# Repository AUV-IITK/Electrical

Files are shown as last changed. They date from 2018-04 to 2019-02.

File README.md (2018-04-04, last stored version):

# Hyperion-Electrical

The repo contains all the schematics, PCB designs, simulations and other files related to Electrical subsystem of AUV-IITK including both past and current projects. A short description of every subdirectory is provided below in the reverse chronological order.

## actuator_board_v1.0 
The team is set to design and fabricate a single PCB for all the drivers that are needed for the actuators in the vehicle. The board also contains a slightly modified version and custom layout of Arduino Mega 2560's [reference design](https://www.arduino.cc/en/uploads/Main/arduino-mega2560-schematic.pdf?). Other than that, the following components form the crux of the board:

[MC34932](https://www.nxp.com/docs/en/data-sheet/MC34932.pdf) Dual H-Bridge Motor Driver to drive [BTD150 Thrusters](http://ocean-innovations.net/OceanInnovationsNEW/SeaBotix/BTD150_Data_Sheet.pdf) from SeaBotix

[Basic ESC R3](http://docs.bluerobotics.com/bescr3/) ESC from BlueRobotics to drive [T200 Thrusters](https://www.bluerobotics.com/store/thrusters/t200-thruster/) also from BlueRobotics

[DRV102](http://www.ti.com/product/DRV102) PWM Solenoid driver from Texas Instruments to control solenoid operated valves

## actuator_board_v0.1
This board is a prototype board intended to test the [MC34932](https://www.nxp.com/docs/en/data-sheet/MC34932.pdf) motor drivers and [Atmega2560](http://ww1.microchip.com/downloads/en/DeviceDoc/Atmel-2549-8-bit-AVR-Microcontroller-ATmega640-1280-1281-2560-2561_datasheet.pdf) circuit independently and observe their individual behavior before integrating them into v1.0 board. The board was fabricated and tested and it worked successfully. The team is moved onto designing the v1.0 board.

## BMSv2
This board is a concept-design of a Battery Management System to control, monitor and protect the Lithium Polymer batteries used in the vehicle. This board has not been fabricated due to technical difficulties we faced while testing the ICs. The following components are used in the board:

[Atxmega128A1U](http://ww1.microchip.com/downloads/en/DeviceDoc/Atmel-8385-8-and-16-bit-AVR-Microcontroller-ATxmega64A1U-ATxmega128A1U_datasheet.pdf) microcontroller as the brain of the board

[BQ76930](http://www.ti.com/lit/ds/symlink/bq76920.pdf) and [BQ78350-R1](https://www.ti.com/lit/ds/symlink/bq78350-r1.pdf?HQS=TI-null-null-sf-df-ds-null-wwe) battery management ICs from Texas Instruments

[TPS54531](http://www.ti.com/lit/ds/symlink/tps54531.pdf) Step Down DC-DC converters to create two voltage rails at 3.3V (to power the Atxmega chip) and 15V (To power an [Intel NUC](https://www.intel.in/content/www/in/en/products/boards-kits/nuc/kits/nuc5i7ryh.html) which is the main on-board computer in the vehicle). The board also provides an unregulated rail to power the [BTD150 Thrusters](http://ocean-innovations.net/OceanInnovationsNEW/SeaBotix/BTD150_Data_Sheet.pdf)

[ACS725](https://www.allegromicro.com/en/Products/Current-Sensor-ICs/Zero-To-Fifty-Amp-Integrated-Conductor-Sensor-ICs/ACS725.aspx) Current Sensors to monitor the current in each of the three rails

## BMS
This is a rudimentary battery management board that was created to act as a back-plane to connect multiple third-party modules. The board has been fabricated and tested and it worked succesfully. The board, however, didn't make it into the vehicle due to its large size.

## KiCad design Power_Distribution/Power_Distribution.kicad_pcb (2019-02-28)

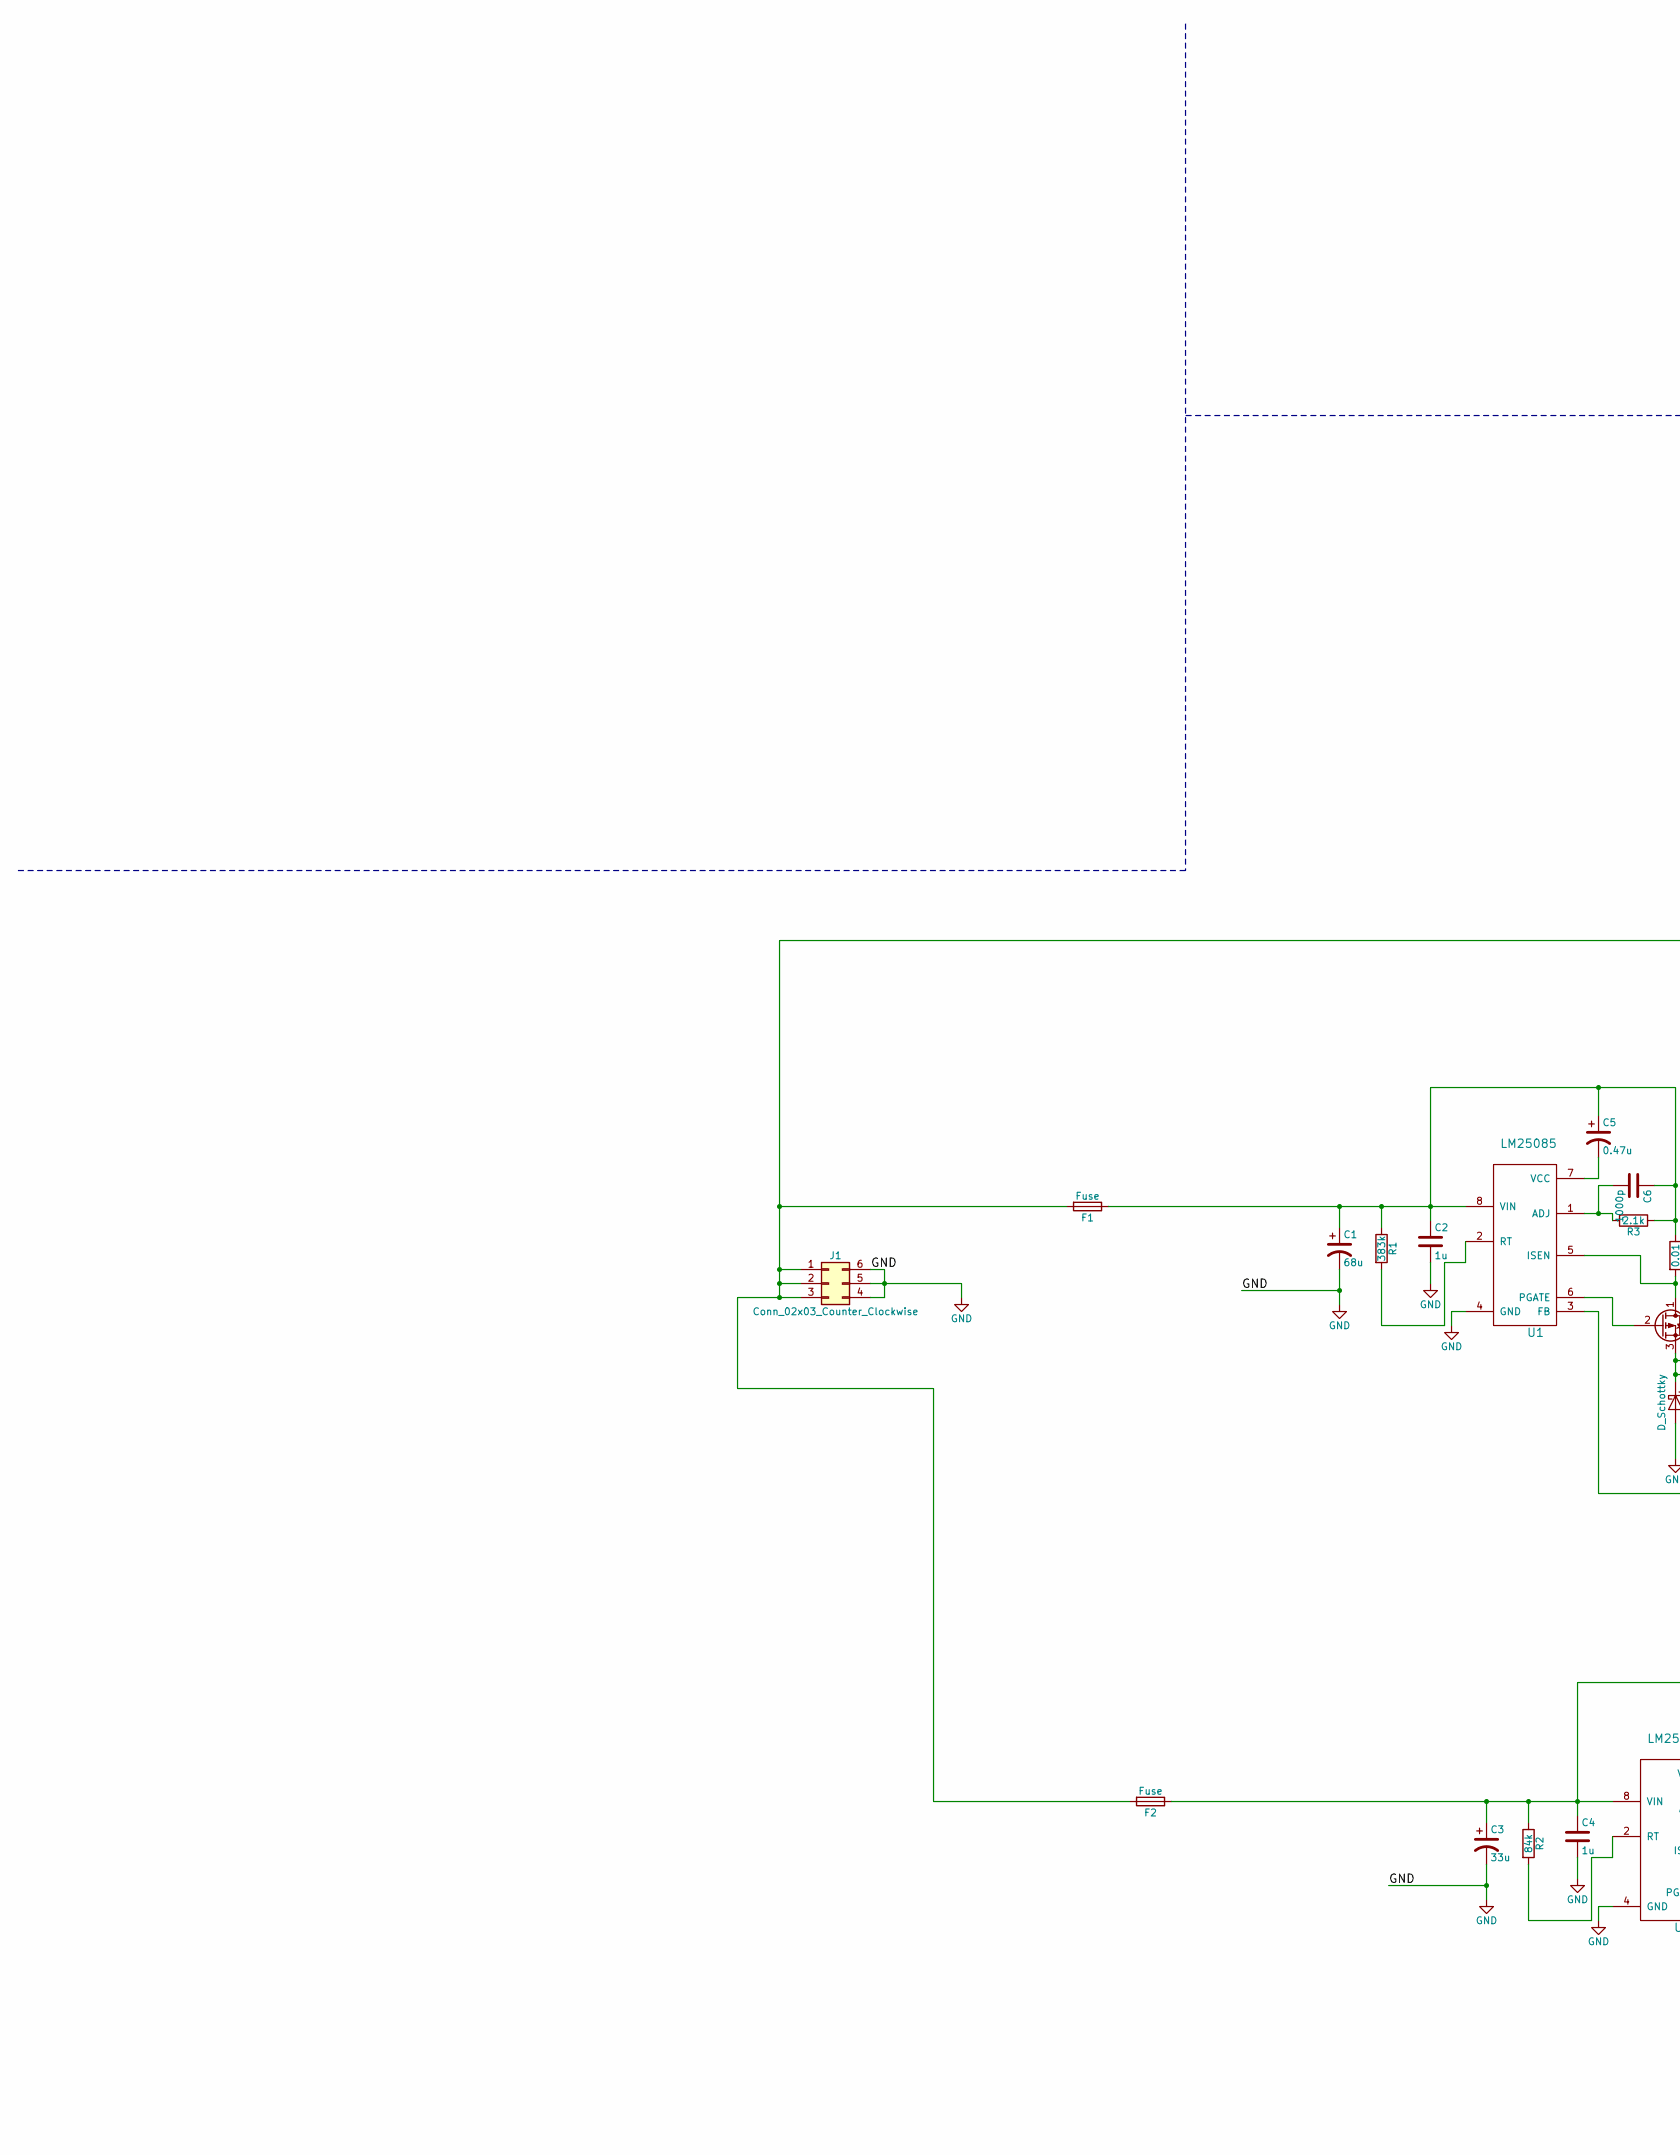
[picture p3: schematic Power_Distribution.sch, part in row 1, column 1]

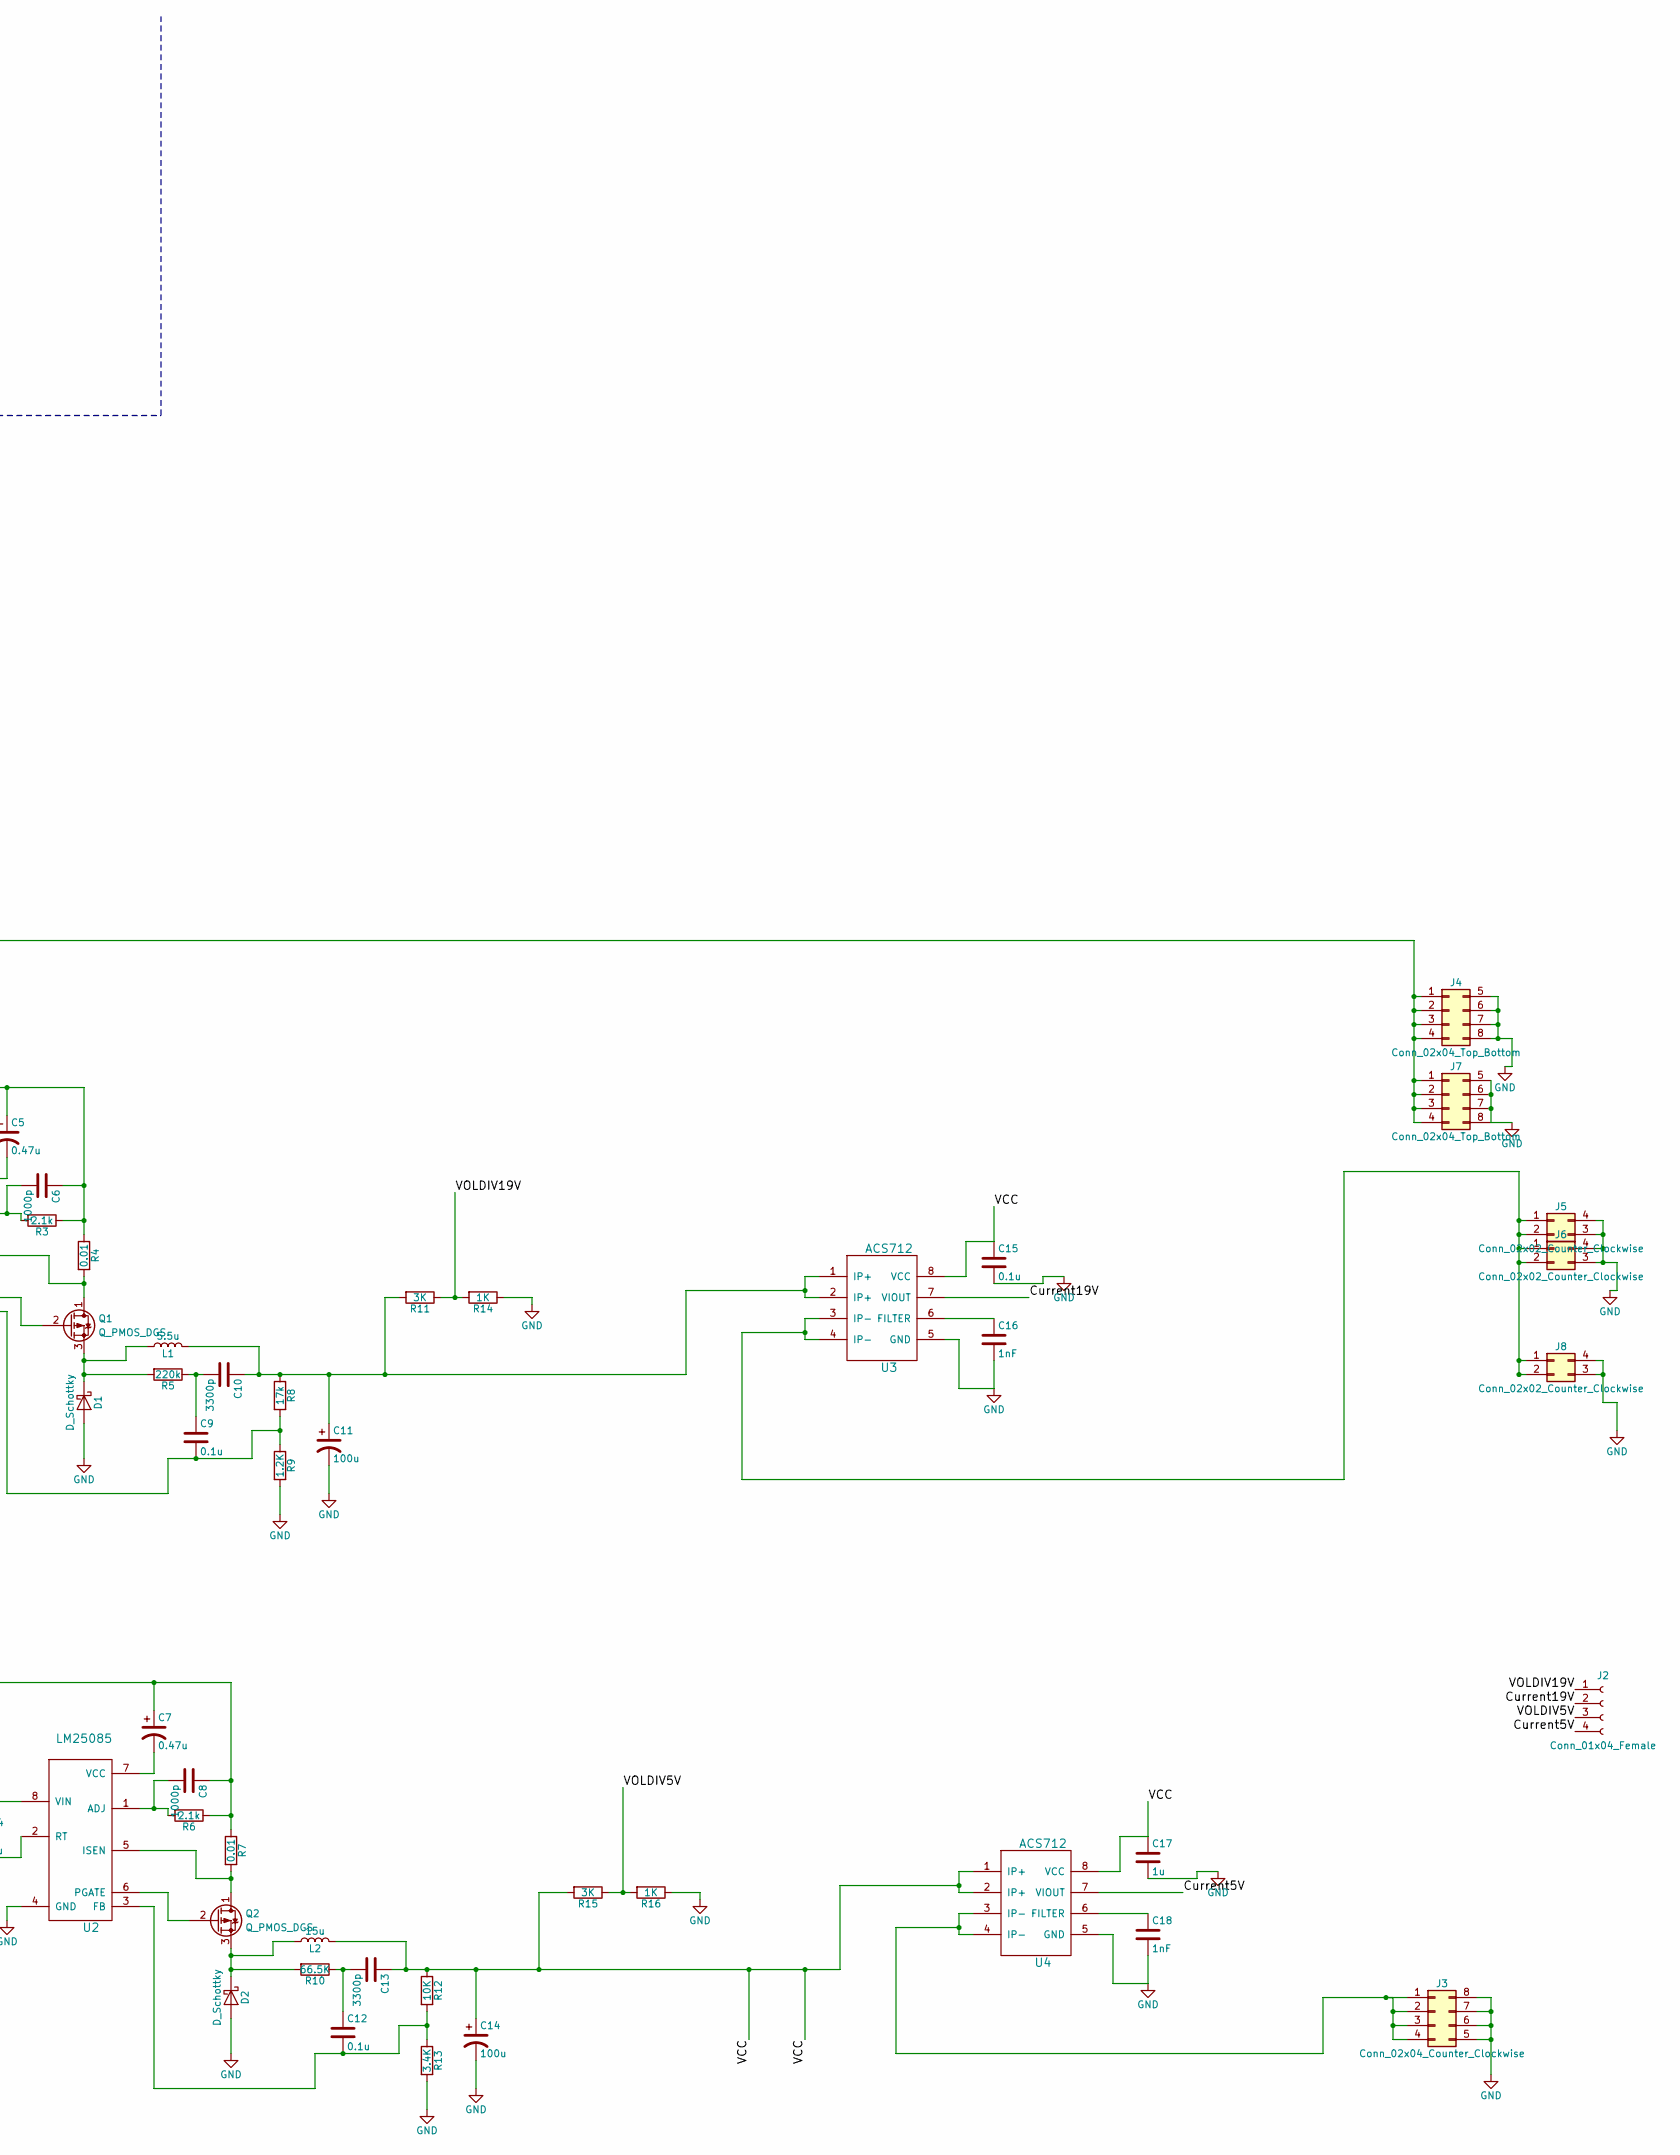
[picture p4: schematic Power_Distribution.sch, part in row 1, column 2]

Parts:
C1: 68u; CP_Radial_D6.3mm_P2.50mm
C2, C4, C17: 1u; C_1206
C3: 33u; CP_Radial_D6.3mm_P2.50mm
C5, C7: 0.47u; CP_Radial_D5.0mm_P2.00mm
C6, C8: 1000p; C_1206
C9, C12, C15: 0.1u; C_1206
C10, C13: 3300p; C_1206
C11, C14: 100u; CP_Radial_D8.0mm_P3.50mm
C16, C18: 1nF; C_1206
D1, D2: D_Schottky; TO-220-2_Vertical
F1, F2: Fuse; Fuse_SMD1206_Wave
J1: Conn_02x03_Counter_Clockwise; Molex_MegaFit_2x03x5.70mm_Straight
J2: Conn_01x04_Female; Molex_PicoClasp_501331-0407_1x04_P1.0mm_Vertical
J3: Conn_02x04_Counter_Clockwise; Molex_MegaFit_2x04x5.70mm_Straight
J4, J7: Conn_02x04_Top_Bottom; Molex_MegaFit_2x04x5.70mm_Straight
J5, J6, J8: Conn_02x02_Counter_Clockwise; Molex_MegaFit_2x02x5.70mm_Straight
L1: 5.5u; L_10.4x10.4_H4.8
L2: 15u; inductor_13.5x12.5
Q1, Q2: Q_PMOS_DGS; TO-252-3_TabPin2
R1: 383k; R_1206
R2: 84k; R_1206
R3, R6: 2.1k; R_1206
R4, R7: 0.01; R_1206
R5: 220k; R_1206
R8: 17k; R_1206
R9: 1.2K; R_1206
R10: 66.5K; R_1206
R11, R15: 3K; R_1206
R12: 10K; R_1206
R13: 3.4K; R_1206
R14, R16: 1K; R_1206
U1, U2: LM25085; VSSOP-8_3.0x3.0mm_Pitch0.65mm
U3, U4: ACS712; SOIC-8_3.9x4.9mm_Pitch1.27mm

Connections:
/Current5V: J2.4, U4.7 (VIOUT)
/Current19V: J2.2, U3.7 (VIOUT)
/VCC: C13.1, C14.1, C15.1, C17.1, L2.2, R12.1, R15.2, U3.8 (VCC), U4.1 (IP+), U4.2 (IP+), U4.8 (VCC)
/VOLDIV5V: J2.3, R15.1, R16.2
/VOLDIV19V: J2.1, R11.1, R14.2
GND: C1.2, C2.2, C3.2, C4.2, C11.2, C14.2, C15.2, C16.2, C17.2, C18.2, D1.2 (A), D2.2 (A), J1.4, J1.5, J1.6, J3.5, J3.6, J3.7, J3.8, J4.5, J4.6, J4.7, J4.8, J5.3, J5.4, J6.3, J6.4, J7.5, J7.6, J7.7, J7.8, J8.3, J8.4, R9.2, R13.2, R14.1, R16.1, U1.4 (GND), U2.4 (GND), U3.5 (GND), U4.5 (GND)
unnamed: C1.1, C2.1, C5.1, C6.1, F1.1, R1.1, R3.1, R4.1, U1.8 (VIN)
unnamed: C3.1, C4.1, C7.1, C8.1, F2.1, R2.1, R6.1, R7.1, U2.8 (VIN)
unnamed: C5.2, U1.7 (VCC)
unnamed: C6.2, R3.2, U1.1 (ADJ)
unnamed: C7.2, U2.7 (VCC)
unnamed: C8.2, R6.2, U2.1 (ADJ)
unnamed: C9.2, R8.2, R9.1, U1.3 (FB)
unnamed: C10.1, C11.1, L1.2, R8.1, R11.2, U3.1 (IP+), U3.2 (IP+)
unnamed: C9.1, C10.2, R5.1
unnamed: C12.1, C13.2, R10.1
unnamed: C12.2, R12.2, R13.1, U2.3 (FB)
unnamed: C16.1, U3.6 (FILTER)
unnamed: C18.1, U4.6 (FILTER)
unnamed: D1.1 (K), L1.1, Q1.3 (S), R5.2
unnamed: D2.1 (K), L2.1, Q2.3 (S), R10.2
unnamed: F1.2, F2.2, J1.1, J1.2, J1.3, J4.1, J4.2, J4.3, J4.4, J7.1, J7.2, J7.3, J7.4
unnamed: J3.1, J3.2, J3.3, J3.4, U4.3 (IP-), U4.4 (IP-)
unnamed: J5.1, J5.2, J6.1, J6.2, J8.1, J8.2, U3.3 (IP-), U3.4 (IP-)
unnamed: Q1.1 (D), R4.2, U1.5 (ISEN)
unnamed: Q1.2 (G), U1.6 (PGATE)
unnamed: Q2.1 (D), R7.2, U2.5 (ISEN)
unnamed: Q2.2 (G), U2.6 (PGATE)
unnamed: R1.2, U1.2 (RT)
unnamed: R2.2, U2.2 (RT)

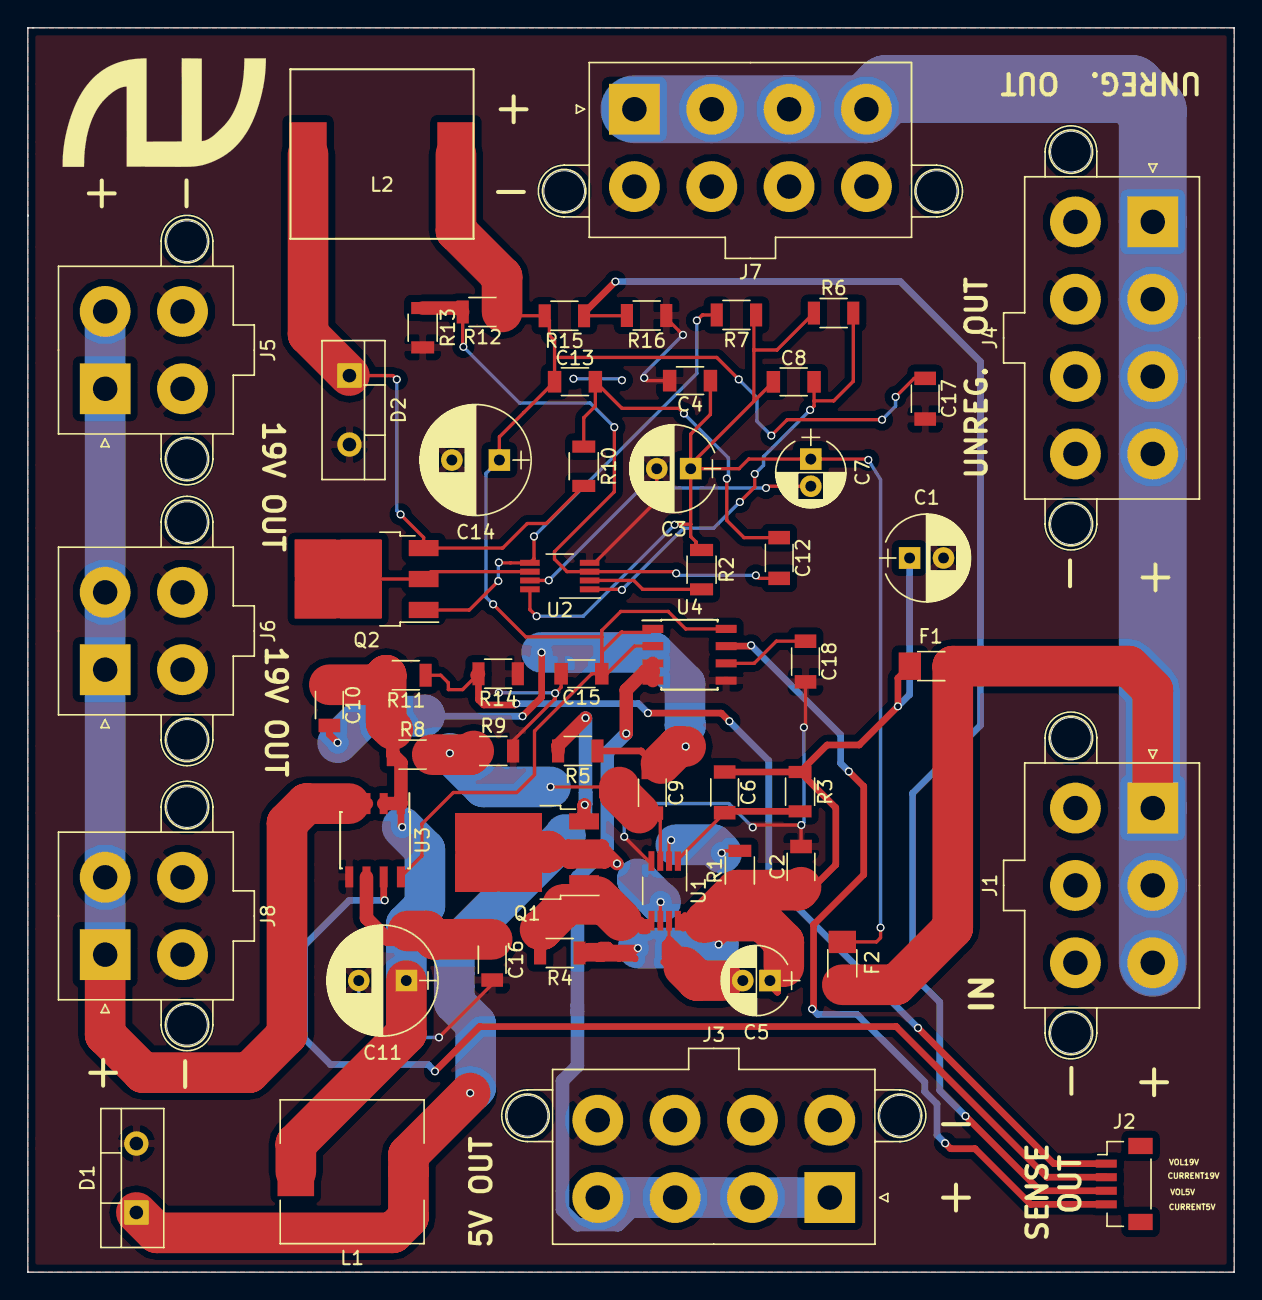
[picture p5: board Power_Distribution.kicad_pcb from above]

Board: 2 copper layers, 88.9 x 91.7 mm, 54 parts (0 on the bottom side), 30 nets.

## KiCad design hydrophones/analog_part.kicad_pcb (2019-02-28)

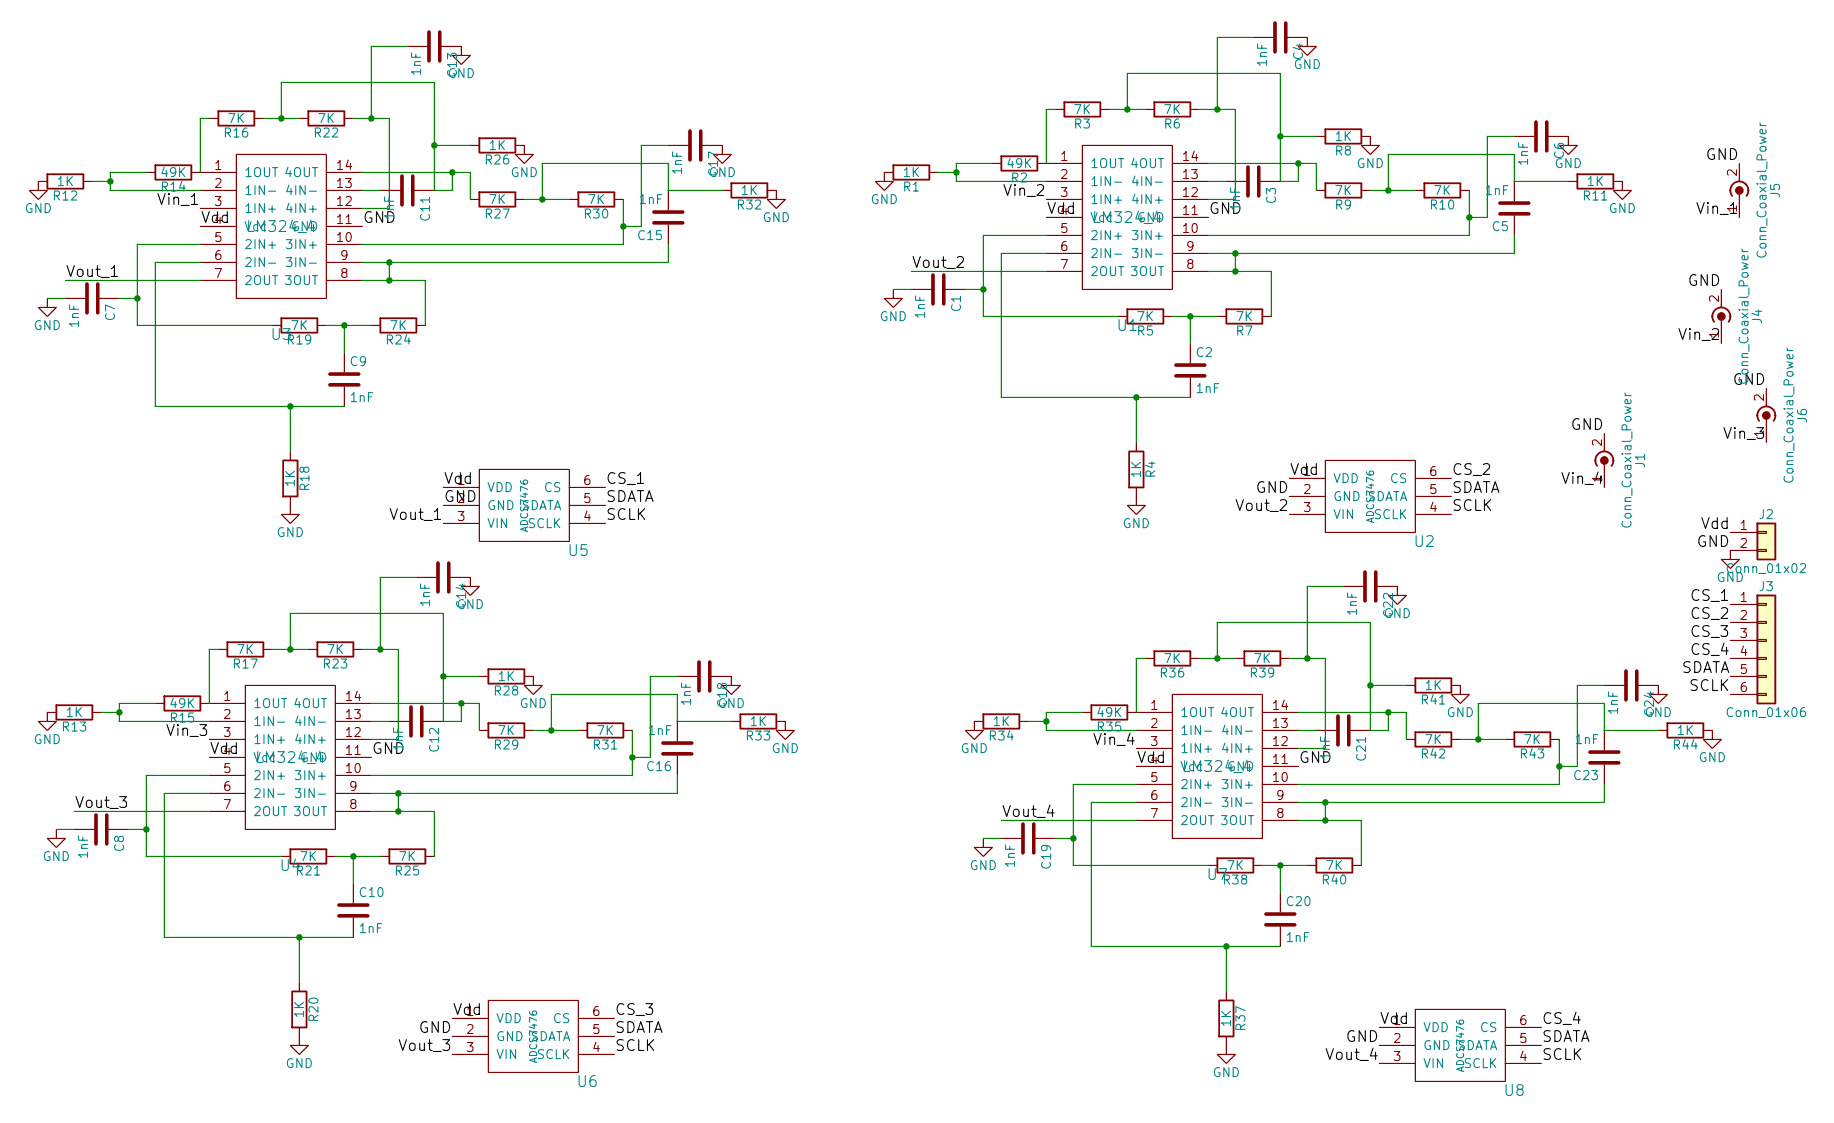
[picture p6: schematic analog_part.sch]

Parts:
C1, C2, C3, C4, C5, C6, C7, C8, C9, C10, C11, C12, C13, C14, C15, C16, C17, C18, C19, C20, C21, C22, C23, C24: 1nF; C_1206_HandSoldering
J1, J4, J5, J6: Conn_Coaxial_Power; bnc-ci
J2: Conn_01x02; Pin_Header_Angled_1x02_Pitch2.54mm
J3: Conn_01x06; Pin_Header_Angled_1x06_Pitch2.54mm
R1, R4, R8, R11, R12, R13, R18, R20, R26, R28, R32, R33, R34, R37, R41, R44: 1K; R_1206_HandSoldering
R2, R14, R15, R35: 49K; R_1206_HandSoldering
R3, R5, R6, R7, R9, R10, R16, R17, R19, R21, R22, R23, R24, R25, R27, R29, R30, R31, R36, R38, R39, R40, R42, R43: 7K; R_1206_HandSoldering
U1, U3, U4, U7: LM324_4; TSSOP-14_4.4x5mm_Pitch0.65mm
U2, U5, U6, U8: ADCS7476; SOT-23-6_Handsoldering

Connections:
/CS_1: J3.1, U5.6 (CS)
/CS_2: J3.2, U2.6 (CS)
/CS_3: J3.3, U6.6 (CS)
/CS_4: J3.4, U8.6 (CS)
/SCLK: J3.6, U2.4 (SCLK), U5.4 (SCLK), U6.4 (SCLK), U8.4 (SCLK)
/SDATA: J3.5, U2.5 (SDATA), U5.5 (SDATA), U6.5 (SDATA), U8.5 (SDATA)
/Vdd: J2.1, U1.4 (Vcc), U2.1 (VDD), U3.4 (Vcc), U4.4 (Vcc), U5.1 (VDD), U6.1 (VDD), U7.4 (Vcc), U8.1 (VDD)
/Vin_1: J5.1 (In), U3.3 (1IN+)
/Vin_2: J4.1 (In), U1.3 (1IN+)
/Vin_3: J6.1 (In), U4.3 (1IN+)
/Vin_4: J1.1 (In), U7.3 (1IN+)
/Vout_1: U3.7 (2OUT), U5.3 (VIN)
/Vout_2: U1.7 (2OUT), U2.3 (VIN)
/Vout_3: U4.7 (2OUT), U6.3 (VIN)
/Vout_4: U7.7 (2OUT), U8.3 (VIN)
GND: C1.2, C4.1, C6.1, C7.2, C8.2, C13.1, C14.1, C17.1, C18.1, C19.2, C22.1, C24.1, J1.2 (Ext), J2.2, J4.2 (Ext), J5.2 (Ext), J6.2 (Ext), R1.2, R4.2, R8.1, R11.1, R12.2, R13.2, R18.2, R20.2, R26.1, R28.1, R32.1, R33.1, R34.2, R37.2, R41.1, R44.1, U1.11 (GND), U2.2 (GND), U3.11 (GND), U4.11 (GND), U5.2 (GND), U6.2 (GND), U7.11 (GND), U8.2 (GND)
unnamed: C1.1, R5.2, U1.5 (2IN+)
unnamed: C2.1, R5.1, R7.2
unnamed: C2.2, R4.1, U1.6 (2IN-)
unnamed: C3.1, R3.1, R6.2, R8.2, R9.2, U1.14 (4OUT)
unnamed: C3.2, U1.13 (4IN-)
unnamed: C4.2, R6.1, U1.12 (4IN+)
unnamed: C5.1, R7.1, U1.8 (3OUT), U1.9 (3IN-)
unnamed: C5.2, R9.1, R10.2, R11.2
unnamed: C6.2, R10.1, U1.10 (3IN+)
unnamed: C7.1, R19.2, U3.5 (2IN+)
unnamed: C8.1, R21.2, U4.5 (2IN+)
unnamed: C9.1, R19.1, R24.2
unnamed: C9.2, R18.1, U3.6 (2IN-)
unnamed: C10.1, R21.1, R25.2
unnamed: C10.2, R20.1, U4.6 (2IN-)
unnamed: C11.1, R16.1, R22.2, R26.2, R27.2, U3.14 (4OUT)
unnamed: C11.2, U3.13 (4IN-)
unnamed: C12.1, R17.1, R23.2, R28.2, R29.2, U4.14 (4OUT)
unnamed: C12.2, U4.13 (4IN-)
unnamed: C13.2, R22.1, U3.12 (4IN+)
unnamed: C14.2, R23.1, U4.12 (4IN+)
unnamed: C15.1, R24.1, U3.8 (3OUT), U3.9 (3IN-)
unnamed: C15.2, R27.1, R30.2, R32.2
unnamed: C16.1, R25.1, U4.8 (3OUT), U4.9 (3IN-)
unnamed: C16.2, R29.1, R31.2, R33.2
unnamed: C17.2, R30.1, U3.10 (3IN+)
unnamed: C18.2, R31.1, U4.10 (3IN+)
unnamed: C19.1, R38.2, U7.5 (2IN+)
unnamed: C20.1, R38.1, R40.2
unnamed: C20.2, R37.1, U7.6 (2IN-)
unnamed: C21.1, R36.1, R39.2, R41.2, R42.2, U7.14 (4OUT)
unnamed: C21.2, U7.13 (4IN-)
unnamed: C22.2, R39.1, U7.12 (4IN+)
unnamed: C23.1, R40.1, U7.8 (3OUT), U7.9 (3IN-)
unnamed: C23.2, R42.1, R43.2, R44.2
unnamed: C24.2, R43.1, U7.10 (3IN+)
unnamed: R1.1, R2.2, U1.2 (1IN-)
unnamed: R2.1, R3.2, U1.1 (1OUT)
unnamed: R12.1, R14.2, U3.2 (1IN-)
unnamed: R13.1, R15.2, U4.2 (1IN-)
unnamed: R14.1, R16.2, U3.1 (1OUT)
unnamed: R15.1, R17.2, U4.1 (1OUT)
unnamed: R34.1, R35.2, U7.2 (1IN-)
unnamed: R35.1, R36.2, U7.1 (1OUT)

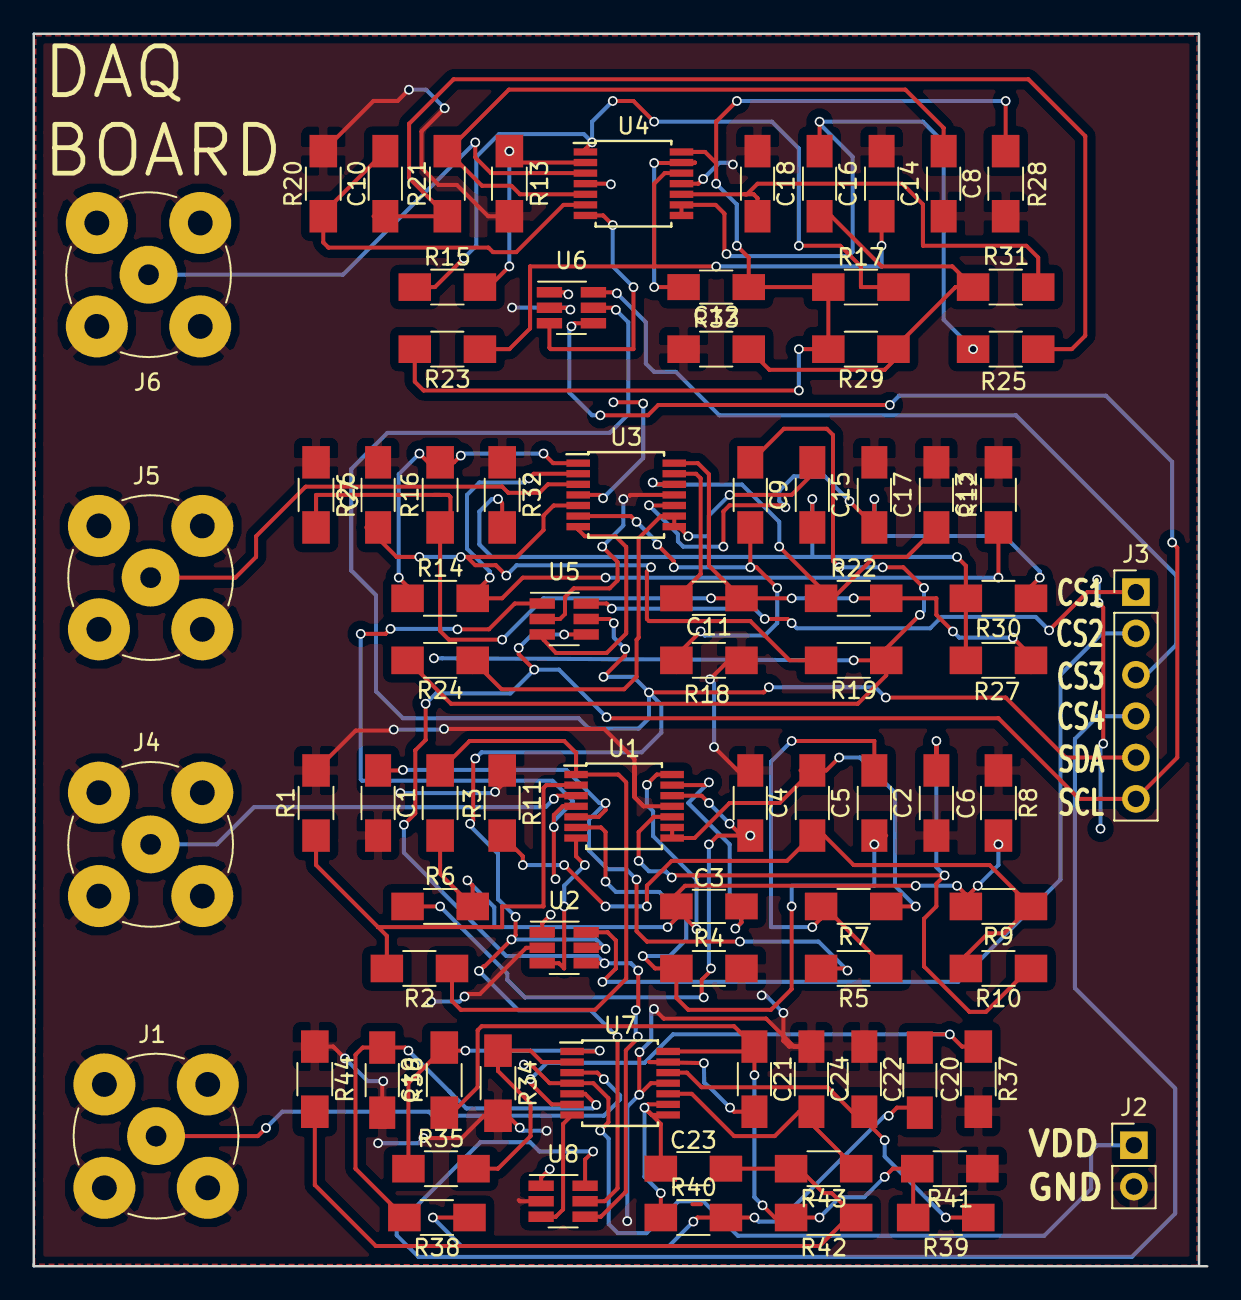
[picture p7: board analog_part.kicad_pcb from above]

Board: 2 copper layers, 72.1 x 75.7 mm, 82 parts (0 on the bottom side), 60 nets.

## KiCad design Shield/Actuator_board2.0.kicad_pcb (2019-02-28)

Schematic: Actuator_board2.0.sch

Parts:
J1: Conn_01x05_Male; Pin_Header_Straight_1x05_Pitch2.54mm
J2, J3: Conn_01x13_Female; Socket_Strip_Straight_1x13_Pitch2.54mm
J4, J5, J8, J9, J12: Conn_01x04_Male; Pin_Header_Straight_1x04_Pitch2.54mm
J6: Conn_01x08_Male; Pin_Header_Straight_1x08_Pitch2.54mm
J7: Conn_01x07_Male; Pin_Header_Straight_1x07_Pitch2.54mm
J10, J11: Conn_01x02_Male; Pin_Header_Straight_1x02_Pitch2.54mm
XA1: Arduino_Mega2560_Shield

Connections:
/3.3V: J1.5, J11.1, J11.2, XA1.3V3 (3.3V)
/5V: J1.3, J4.1, J4.2, J4.3, J4.4, XA1.5V1 (5V)
/ANA1: J12.1, XA1.A4
/ANA2: J12.2, XA1.A5
/ANA3: J12.3, XA1.A6
/ANA4: J12.4, XA1.A7
/CS-1: J2.3, XA1.A0
/CS-2: J2.10, XA1.A1
/CS-3: J3.3, XA1.A2
/CS-4: J3.10, XA1.A3
/DIG1: J8.1, XA1.D40
/DIG2: J8.2, XA1.D41
/DIG3: J8.3, XA1.D42
/DIG4: J8.4, XA1.D43
/DIRA-1: J2.5, XA1.D22
/DIRA-2: J2.12, XA1.D24
/DIRA-3: J3.5, XA1.D26
/DIRA-4: J3.12, XA1.D28
/DIRB-1: J2.6, XA1.D23
/DIRB-2: J2.13, XA1.D25
/DIRB-3: J3.6, XA1.D27
/DIRB-4: J3.13, XA1.D29
/GND: J1.4, J2.1, J2.8, J3.1, J3.8, J5.1, J5.2, J5.3, J5.4, J6.2, J6.4, J6.6, J6.8, J7.7, XA1.GND1 (GND)
/PW1: J9.1, XA1.D6
/PW2: J9.2, XA1.D7
/PW3: J9.3, XA1.D8
/PW4: J9.4, XA1.D11
/PWM-1: J2.4, XA1.D2 (D2_INT0)
/PWM-2: J2.11, XA1.D3 (D3_INT1)
/PWM-3: J3.4, XA1.D4
/PWM-4: J3.11, XA1.D5
/S1: J7.1, XA1.D34
/S2: J7.2, XA1.D35
/S3: J7.3, XA1.D36
/S4: J7.4, XA1.D37
/S5: J7.5, XA1.D38
/S6: J7.6, XA1.D39
/SCL: J1.1, XA1.SCL
/SCL1: J10.2, XA1.D21 (D21_SCL)
/SDA: J1.2, XA1.SDA
/SDA1: J10.1, XA1.D20 (D20_SDA)
/T-5: J6.1, XA1.D30
/T-6: J6.3, XA1.D31
/T-7: J6.5, XA1.D32
/T-8: J6.7, XA1.D33

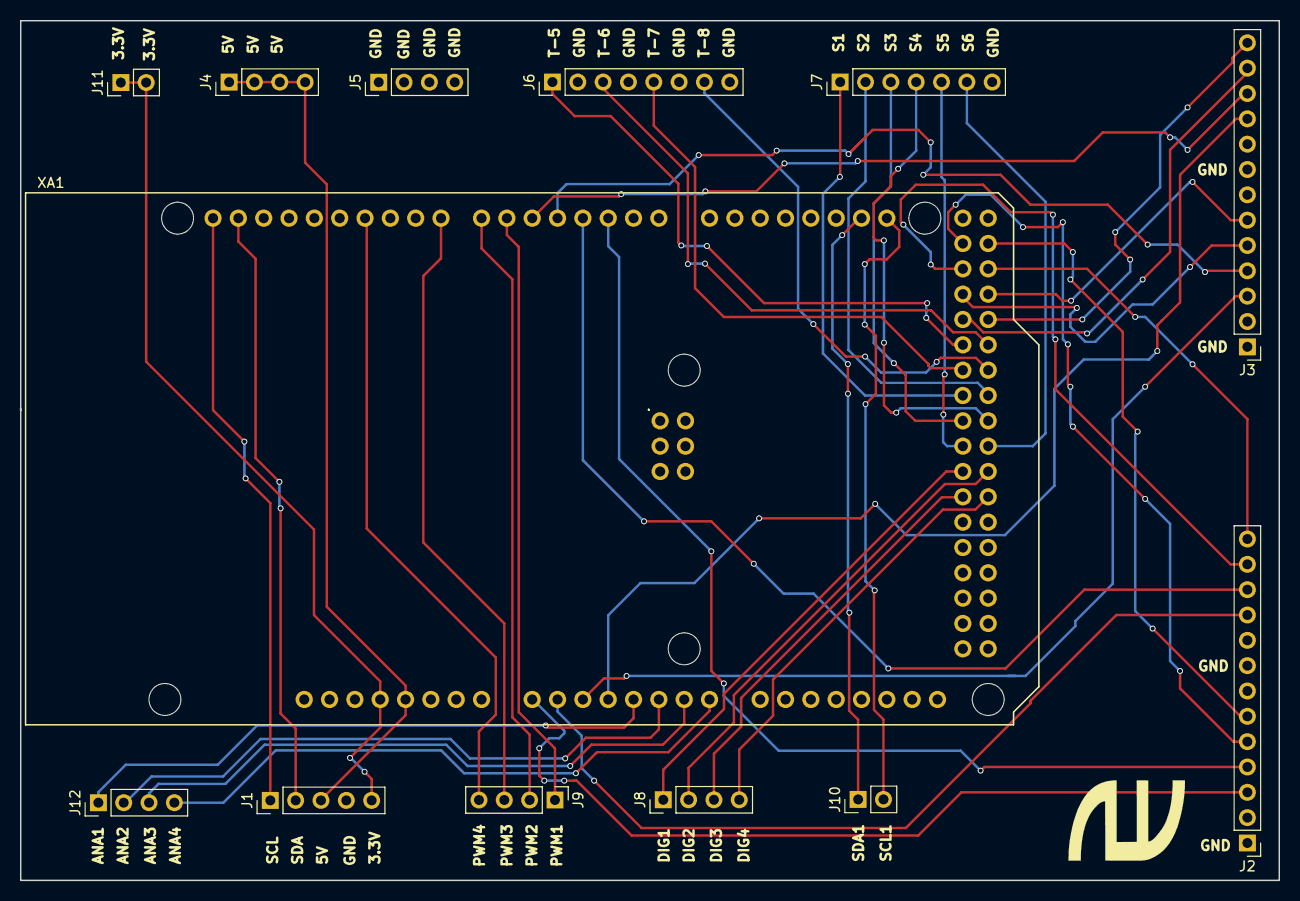
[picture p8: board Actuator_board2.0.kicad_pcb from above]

Board: 2 copper layers, 126.2 x 86.2 mm, 13 parts (0 on the bottom side), 45 nets.

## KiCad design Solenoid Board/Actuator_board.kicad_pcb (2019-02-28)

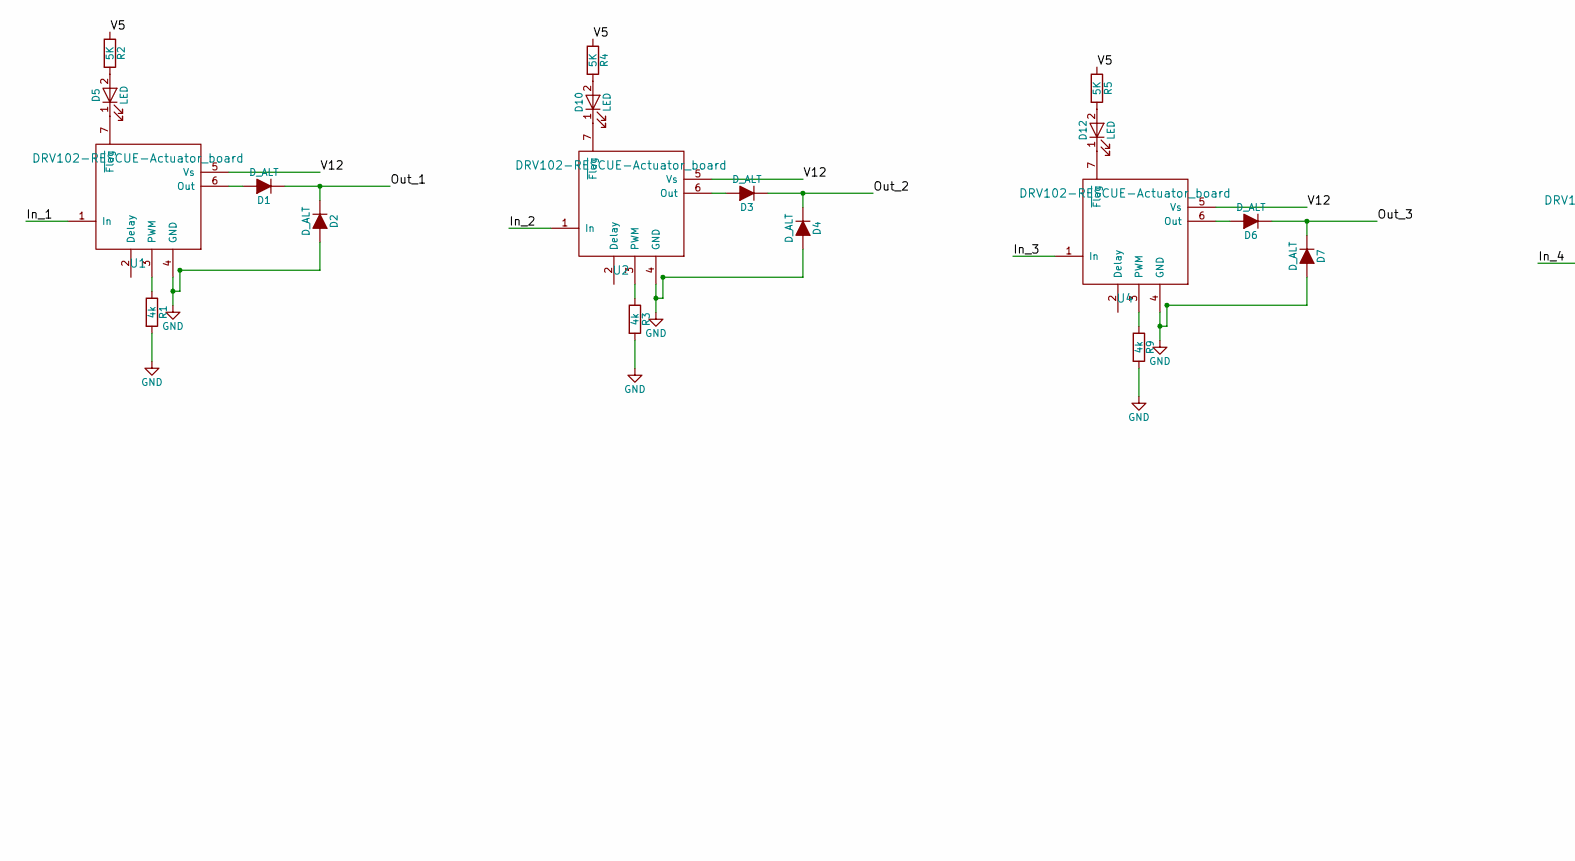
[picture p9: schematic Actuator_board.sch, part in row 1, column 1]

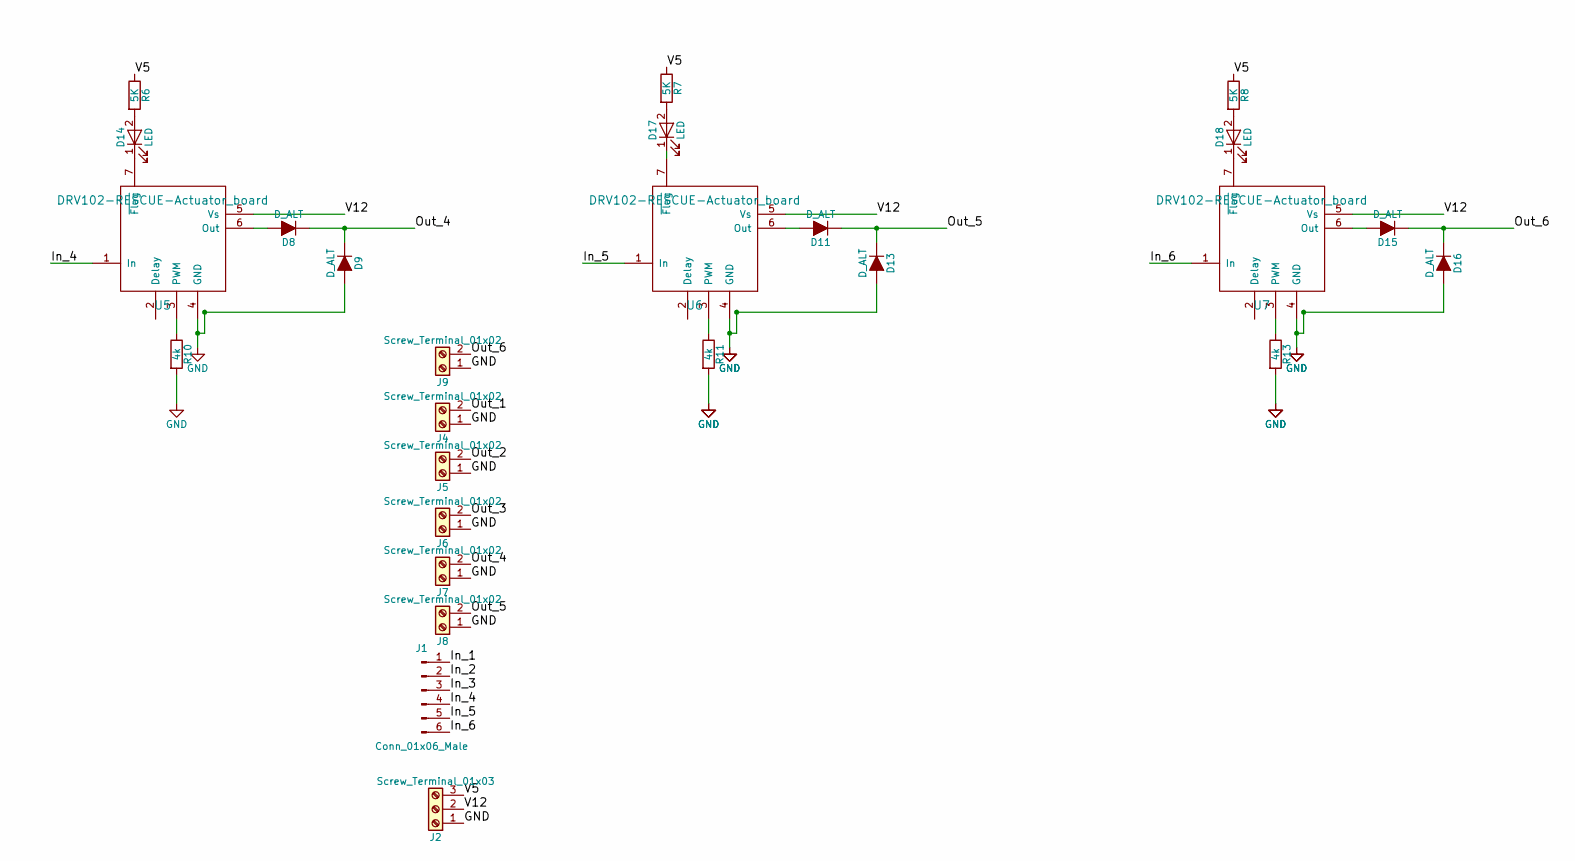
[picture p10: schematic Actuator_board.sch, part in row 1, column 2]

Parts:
D1, D2, D3, D4, D6, D7, D8, D9, D11, D13, D15, D16: D_ALT; DO-214AB
D5: LED; LED_D2.0mm_W4.8mm_H2.5mm_FlatTop
D10, D12, D14, D17, D18: LED; LED_D3.0mm
J1: Conn_01x06_Male; Pin_Header_Straight_1x06_Pitch2.54mm
J2: Screw_Terminal_01x03; TerminalBlock_bornier-3_P5.08mm
J4, J5, J6, J7, J8, J9: Screw_Terminal_01x02; TerminalBlock_bornier-2_P5.08mm
R1, R3, R9, R10, R11, R13: 4k; R_1206
R2, R4, R5, R6, R7, R8: 5K; R_1206
U1, U2, U4, U5, U6, U7: DRV102-RESCUE-Actuator_board; TO-263-7_TabPin4

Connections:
/In_1: J1.1, U1.1 (In)
/In_2: J1.2, U2.1 (In)
/In_3: J1.3, U4.1 (In)
/In_4: J1.4, U5.1 (In)
/In_5: J1.5, U6.1 (In)
/In_6: J1.6, U7.1 (In)
/Out_1: D1.1 (K), D2.1 (K), J4.2
/Out_2: D3.1 (K), D4.1 (K), J5.2
/Out_3: D6.1 (K), D7.1 (K), J6.2
/Out_4: D8.1 (K), D9.1 (K), J7.2
/Out_5: D11.1 (K), D13.1 (K), J8.2
/Out_6: D15.1 (K), D16.1 (K), J9.2
/V5: J2.3, R2.1, R4.1, R5.1, R6.1, R7.1, R8.1
/V12: J2.2, U1.5 (Vs), U2.5 (Vs), U4.5 (Vs), U5.5 (Vs), U6.5 (Vs), U7.5 (Vs)
GND: D2.2 (A), D4.2 (A), D7.2 (A), D9.2 (A), D13.2 (A), D16.2 (A), J2.1, J4.1, J5.1, J6.1, J7.1, J8.1, J9.1, R1.2, R3.2, R9.2, R10.2, R11.2, R13.2, U1.4 (GND), U2.4 (GND), U4.4 (GND), U5.4 (GND), U6.4 (GND), U7.4 (GND)
unnamed: D1.2 (A), U1.6 (Out)
unnamed: D3.2 (A), U2.6 (Out)
unnamed: D5.1 (K), U1.7 (~Flag)
unnamed: D5.2 (A), R2.2
unnamed: D6.2 (A), U4.6 (Out)
unnamed: D8.2 (A), U5.6 (Out)
unnamed: D10.1 (K), U2.7 (~Flag)
unnamed: D10.2 (A), R4.2
unnamed: D11.2 (A), U6.6 (Out)
unnamed: D12.1 (K), U4.7 (~Flag)
unnamed: D12.2 (A), R5.2
unnamed: D14.1 (K), U5.7 (~Flag)
unnamed: D14.2 (A), R6.2
unnamed: D15.2 (A), U7.6 (Out)
unnamed: D17.1 (K), U6.7 (~Flag)
unnamed: D17.2 (A), R7.2
unnamed: D18.1 (K), U7.7 (~Flag)
unnamed: D18.2 (A), R8.2
unnamed: R1.1, U1.3 (PWM)
unnamed: R3.1, U2.3 (PWM)
unnamed: R9.1, U4.3 (PWM)
unnamed: R10.1, U5.3 (PWM)
unnamed: R11.1, U6.3 (PWM)
unnamed: R13.1, U7.3 (PWM)

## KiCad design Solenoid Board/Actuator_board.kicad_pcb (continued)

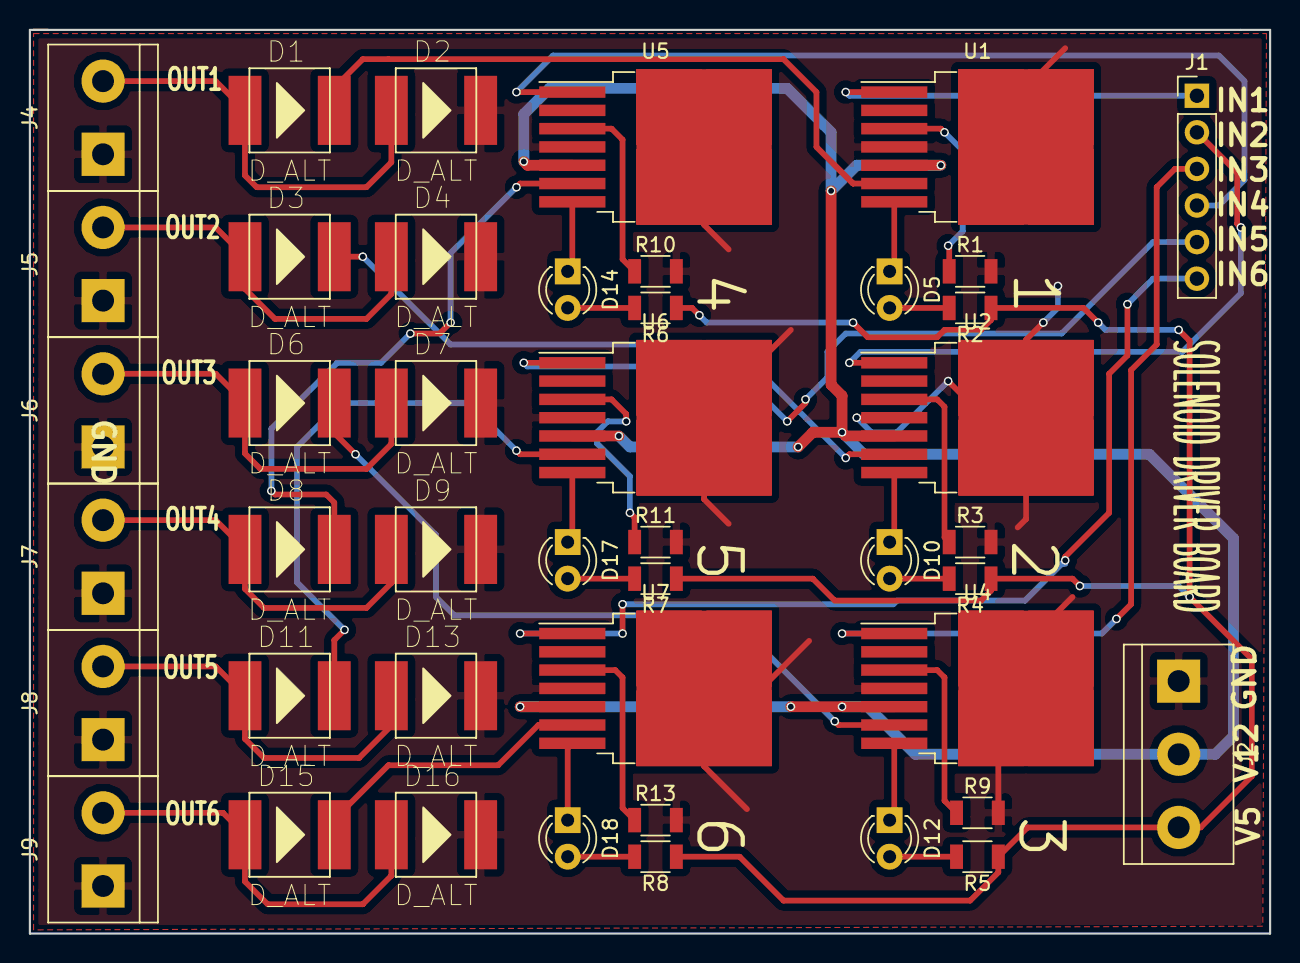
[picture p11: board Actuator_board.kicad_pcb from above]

Board: 2 copper layers, 86.1 x 62.7 mm, 44 parts (0 on the bottom side), 39 nets.

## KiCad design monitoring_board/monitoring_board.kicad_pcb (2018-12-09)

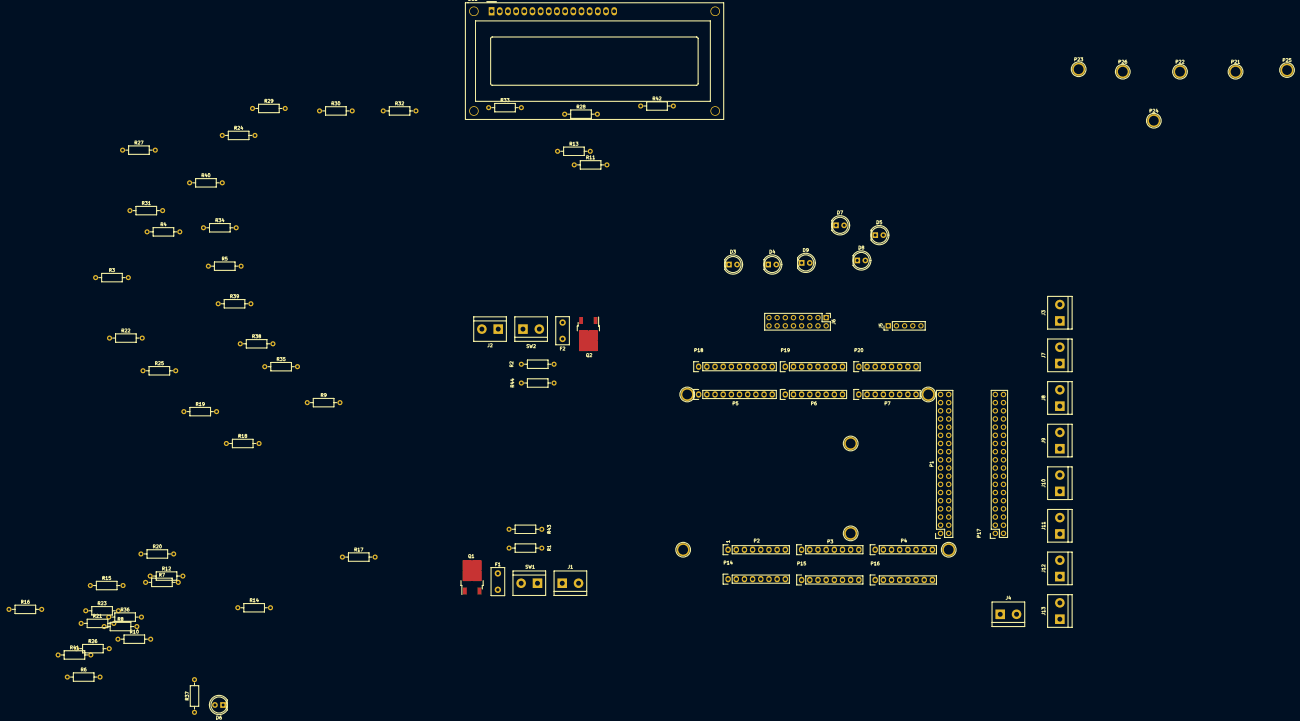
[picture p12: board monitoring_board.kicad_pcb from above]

Board: 2 copper layers, 97 parts (0 on the bottom side), 107 nets, no tracks yet.

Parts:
D3, D4, D5, D6, D7, D8, D9: LED; LED_D5.0mm
DS1: WC1602A
F1: 30A Polyfuse; Fuse_TE5_Littlefuse-395Series
F2: 4A Polyfuse; Fuse_TE5_Littlefuse-395Series
J1, J2, J3, J4, J7, J8, J9, J10, J11, J12, J13: Conn_01x02; TerminalBlock_bornier-2_P5.08mm
J5: Conn_01x05; Pin_Header_Straight_1x05_Pitch2.54mm
J6: Conn_02x08_Odd_Even; Pin_Header_Straight_2x08_Pitch2.54mm
P1, P17: Digital; Socket_Strip_Arduino_2x18
P2, P14: Power; Socket_Strip_Arduino_1x08
P3, P4, P15, P16: Analog; Socket_Strip_Arduino_1x08
P5, P18: PWM; Socket_Strip_Arduino_1x10
P6, P19: PWM; Socket_Strip_Arduino_1x08
P7, P20: Communication; Socket_Strip_Arduino_1x08
P8, P9, P10, P11, P12, P13, P21, P22, P23, P24, P25, P26: CONN_01X01; Arduino_1pin
Q1, Q2: Q_PMOS_GDS; TO-252-2
R1, R2, R13, R15, R17, R19, R21, R23, R25, R27, R29, R31, R33, R34, R35, R36, R37, R38, R39, R40, R43, R44: 1K; R_Axial_DIN0207_L6.3mm_D2.5mm_P10.16mm_Horizontal
R3, R4, R5, R6, R7, R8, R9, R10, R11: 50m; R_Axial_DIN0207_L6.3mm_D2.5mm_P10.16mm_Horizontal
R12, R14, R16, R18, R20, R22, R24, R26, R28, R30, R32: 24K; R_Axial_DIN0207_L6.3mm_D2.5mm_P10.16mm_Horizontal
R41: R; R_Axial_DIN0207_L6.3mm_D2.5mm_P10.16mm_Horizontal
R42: 220; R_Axial_DIN0207_L6.3mm_D2.5mm_P10.16mm_Horizontal
SW1, SW2: SW_DIP_x01; TerminalBlock_bornier-2_P5.08mm

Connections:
+3V3: J5.2, P2.4, P14.4
+5V: DS1.2, J5.1, P1.35, P1.36, P2.5, P14.5, P17.35, P17.36, R37.2, R42.1
/0(Rx0): P6.8, P19.8
/1(Tx0): P6.7, P19.7
/2(**): J6.1, P6.6, P19.6
/3(**): J6.3, P6.5, P19.5
/4(**): J6.5, P6.4, P19.4
/5(**): J6.7, P6.3, P19.3
/6(**): J6.9, P6.2, P19.2
/7(**): J6.11, P6.1, P19.1
/8(**): J6.13, P5.10, P18.10
/9(**): J6.15, P5.9, P18.9
/10(**): P5.8, P18.8
/11(**): P5.7, P18.7
/12(**): P5.6, P18.6
/13(**): P5.5, P18.5, R36.2
/14(Tx3): P7.1, P20.1
/15(Rx3): P7.2, P20.2
/16(Tx2): P7.3, P20.3
/17(Rx2): P7.4, P20.4
/18(Tx1): P7.5, P20.5
/19(Rx1): P7.6, P20.6
/20(SDA): J5.3, P7.7, P20.7, R38.2
/21(SCL): J5.4, P7.8, P20.8, R39.2
/22: P1.33, P17.33, R40.2
/23: DS1.11, P1.34, P17.34
/24: DS1.12, P1.31, P17.31
/25: DS1.13, P1.32, P17.32
/26: DS1.14, P1.29, P17.29
/27: DS1.6, P1.30, P17.30
/28: DS1.4, P1.27, P17.27
/29: P1.28, P17.28
/30: P1.25, P17.25
/31: P1.26, P17.26
/32: P1.23, P17.23
/33: P1.24, P17.24
/34: P1.21, P17.21
/35: P1.22, P17.22
/36: P1.19, P17.19
/37: P1.20, P17.20
/38: P1.17, P17.17
/39: P1.18, P17.18
/40: P1.15, P17.15
/41: P1.16, P17.16
/42: P1.13, P17.13
/43: P1.14, P17.14
/44: P1.11, P17.11
/45: P1.12, P17.12
/46: P1.9, P17.9
/47: P1.10, P17.10
/48: P1.7, P17.7
/49: P1.8, P17.8
/50(MISO): P1.5, P17.5
/51(MOSI): P1.6, P17.6
/52(SCK): P1.3, P17.3
/53(SS): P1.4, P17.4
/A0: P3.1, P15.1, R16.1, R17.2
/A1: P3.2, P15.2, R12.1, R13.2
/A2: P3.3, P15.3, R20.1, R21.2
/A3: P3.4, P15.4, R24.1, R25.2
/A4: P3.5, P15.5, R32.1, R33.2
/A5: P3.6, P15.6, R14.1, R15.2
/A6: P3.7, P15.7, R18.1, R19.2
/A7: P3.8, P15.8, R26.1, R27.2
/A8: P4.1, P16.1, R30.1, R31.2
/A9: P4.2, P16.2, R22.1, R23.2
/A10: P4.3, P16.3, R28.1, R29.2
/A11: P4.4, P16.4
/A12: P4.5, P16.5
/A13: P4.6, P16.6
/A14: P4.7, P16.7
/A15: P4.8, P16.8
/AREF: P5.3, P18.3
/IOREF: P2.2, P14.2
/Reset: P2.3, P14.3
/SCL: P5.1, P18.1
/SDA: P5.2, P18.2
/VBATT1: Q1.2, SW1.2
/VBATT2: Q2.2, SW2.2
/VESC1: J3.1, R4.1, R12.2
/VESC2: J7.1, R5.1, R20.2
/VESC3: J8.1, R6.1, R24.2
/VESC4: J9.1, R7.1, R32.2
/VESC5: J10.1, R8.1, R14.2
/VESC6: J11.1, R9.1, R18.2
/VESC7: J12.1, R10.1, R26.2
/VESC8: J13.1, R11.1, R30.2
/VIN1: F1.1, R4.2, R5.2, R6.2, R7.2, R8.2, R9.2, R10.2, R11.2, R16.2, R34.2
/VIN2: F2.1, R3.2, R22.2, R35.2
/VNUC: J4.1, R3.1, R28.2
/Vin: P2.8, P14.8
GND: D3.1, D4.1, D5.1, D6.1, D7.1, D8.1, D9.1, DS1.1, DS1.5, DS1.16, J1.2, J2.2, J3.2, J4.2, J5.5, J6.2, J6.4, J6.6, J6.8, J6.10, J6.12, J6.14, J6.16, J7.2, J8.2, J9.2, J10.2, J11.2, J12.2, J13.2, P1.1, P1.2, P2.6, P2.7, P5.4, P14.6, P14.7, P17.1, P17.2, P18.4, R1.1, R2.1, R13.1, R15.1, R17.1, R19.1, R21.1, R23.1, R25.1, R27.1, R29.1, R31.1, R33.1, R41.1
unnamed: D3.2, R34.1
unnamed: D4.2, R35.1
unnamed: D5.2, R36.1
unnamed: D6.2, R37.1
unnamed: D7.2, R38.1
unnamed: D8.2, R39.1
unnamed: D9.2, R40.1
unnamed: DS1.3, R41.2
unnamed: DS1.15, R42.2
unnamed: F1.2, Q1.3, R43.2
unnamed: F2.2, Q2.3, R44.2
unnamed: J1.1, SW1.1
unnamed: J2.1, SW2.1
unnamed: Q1.1, R1.2, R43.1
unnamed: Q2.1, R2.2, R44.1

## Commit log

2018-04-04 Move files from personal repo
    [BMS_3.PcbDoc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]
2018-04-10 Schematic update
    [actuator_board_v1.sch]
2018-04-12 Make corrections to the previous commit
    [actuator_board_v1.sch]
2018-04-15 Add motor drivers to the schematic
    [actuator_board_v1.sch]
2018-05-04 Add files via upload
    These are the completed design of pcbs
    [Power_Distribution.kicad_pcb, Power_Distribution.sch]
2018-05-04 This is the pcb design without exposing traces
2018-05-07 This is the tentatively final model of the PCB
    [Power_Distribution_Final.kicad_pcb, Power_Distribution_Final.sch]
2018-11-29 Monitoring board template upload
    [monitoring_board.kicad_pcb, monitoring_board.sch]
2018-11-30 Monitoring board schematic update
    [_saved_monitoring_board.sch]
2018-12-01 Remove unwanted file
    [_saved_monitoring_board.sch]
2018-12-01 Add LCD
    [monitoring_board.sch]
2018-12-02 Monitoring board schematic update and start assigning footprints
    [monitoring_board.sch]
2018-12-06 Monitoring board complete assigning footprints
    [monitoring_board.sch]
2018-12-06 Monitoring board updates
    1. Change 16-pin header for thruster power to 8 2-pin headers
    2. Replace 16-pin header for thruster signal to different 16-pin header
    3. Move components around (this is making the diff so large)
    [monitoring_board.sch]
2018-12-09 Monitoring board: start pcb design
    [monitoring_board.kicad_pcb, monitoring_board.sch]
2019-02-28 Anahita PCBs
    These are the PCBs currently in use in the vehicle
    [Actuator_board-B.Cu.gbr, Actuator_board-B.Mask.gbr, Actuator_board-Edge.Cuts.gbr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]
2019-04-09 Add ltspice simulation files for hydrophones v2 board
